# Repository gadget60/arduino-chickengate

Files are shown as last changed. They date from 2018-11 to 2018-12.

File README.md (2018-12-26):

# arduino-chickengate
Arduino based mechanic door controller

## ...what?
This is a door controller based on an Arduino. It opens a mechanic door of a hen house in the morning and closes it in the evening. That's it, basically. 

## Timing
Current date/time and open/close times are programmable via USB/serial console (need to wake up from power down sleep first by pressing one of the open or close buttons). Due to early sunset in winter time the open/close times are programmable for each month. I use a DS1307 Real Time Clock module, this allows to persist the timetable in its NVRAM.
Available commands:
- `time [hhmm]`: sets the current time
- `date [YYYYMMDD]`: sets the current date
- `gate [MM] [hhmm] [hhmm]`: sets for month MM the open and close times

## Mechanics
The door is openend/closed by a high torque gear motor, driven by a L9110 DC motor driver board. There are two buttons for manual opening/closing the door and two mechanical end switches (top and bottom).

## Power
Main issue is to keep power consumption low, because the controller as well as mechanics are driven by a small solar panel that feeds 4x1.2V rechargeable batteries. First of all, I got rid of the power LED on the ProMicro board by soldering it out. Due to high power consumption of the motor driver board, it is powered off via a transistor when not used. Finally onboard USB is disabled and the ProMicro is set to SLEEP_MODE_PWR_DOWN. Overall this brings power consumption down to around 20uA in idle mode.

## Hardware
- ProMicro Atmega 5V/16MHz (Dev-12640), https://cdn.sparkfun.com/datasheets/Dev/Arduino/Boards/ProMicro16MHzv1.pdf
- DS1307 Real Time Clock module
- L9110 DC motor driver board
- 6V high torque gear motor (ZnDiy-BRY 25GA-6V-80 DC 6V 80rpm)
- Solar panel, 0.5W, max voltage around 9V

## PINS
```
D2  --> I2C data (Realtime clock SDA)
D3  --> I2C clock (Realtime clock SCL)
D7  --> Wake up pin
D6  --> Motor A PWM Speed
D5  --> Motor A Direction
D9  --> Driver Power (Transistor Base)
D14 --> Up button, normally open
D15 --> Down button, normally open
D10 --> End switch top, normally closed
D16 --> End switch bottom, normally closed
```

## Scheme

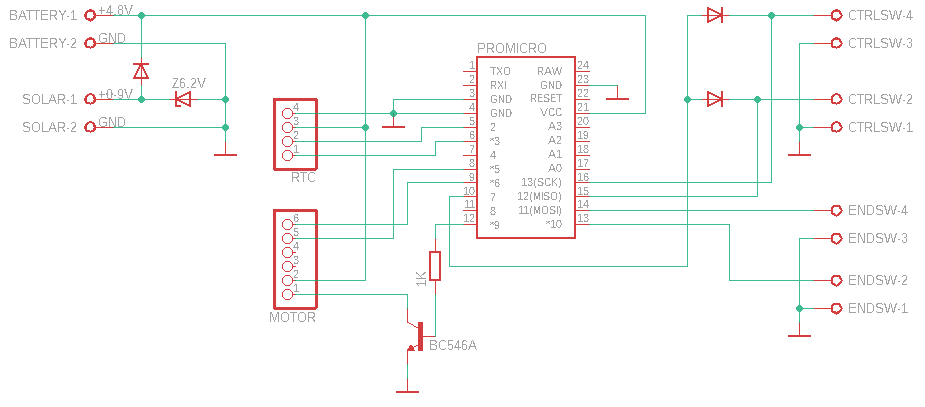
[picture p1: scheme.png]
Scheme


## Images

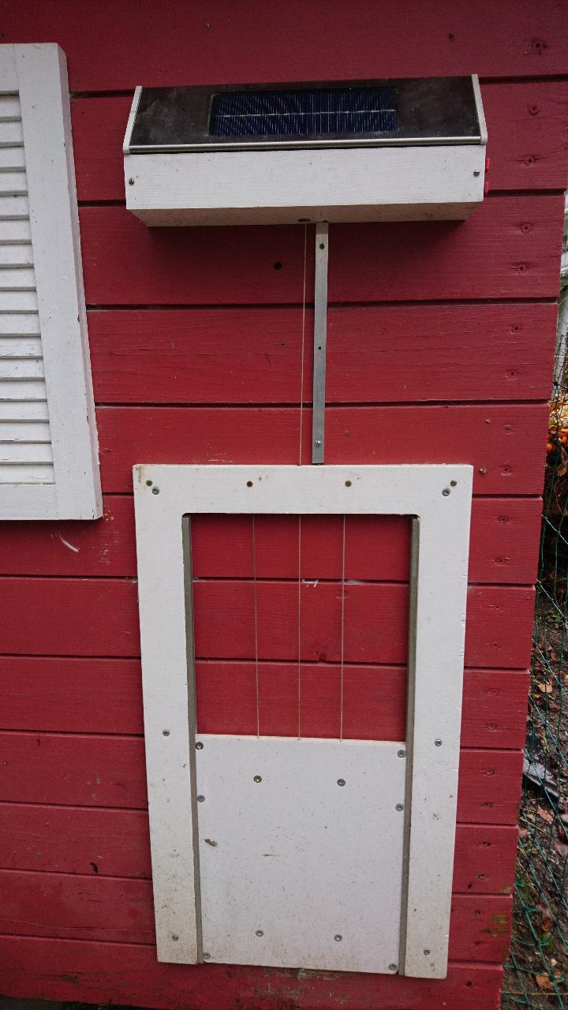
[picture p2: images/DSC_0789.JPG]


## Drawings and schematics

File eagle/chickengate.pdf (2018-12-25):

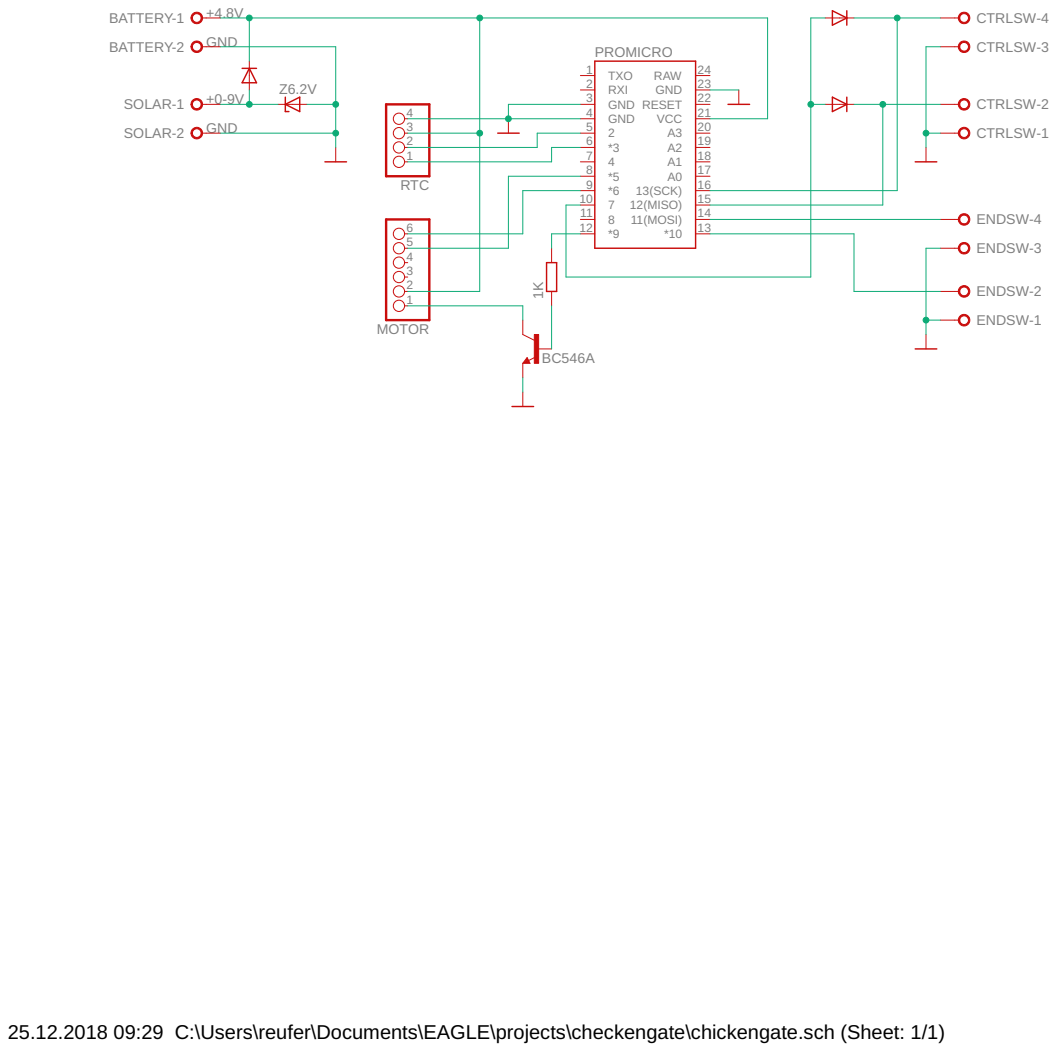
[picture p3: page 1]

25.12.2018 09:29 C:\Users\reufer\Documents\EAGLE\projects\checkengate\chickengate.sch (Sheet: 1/1)

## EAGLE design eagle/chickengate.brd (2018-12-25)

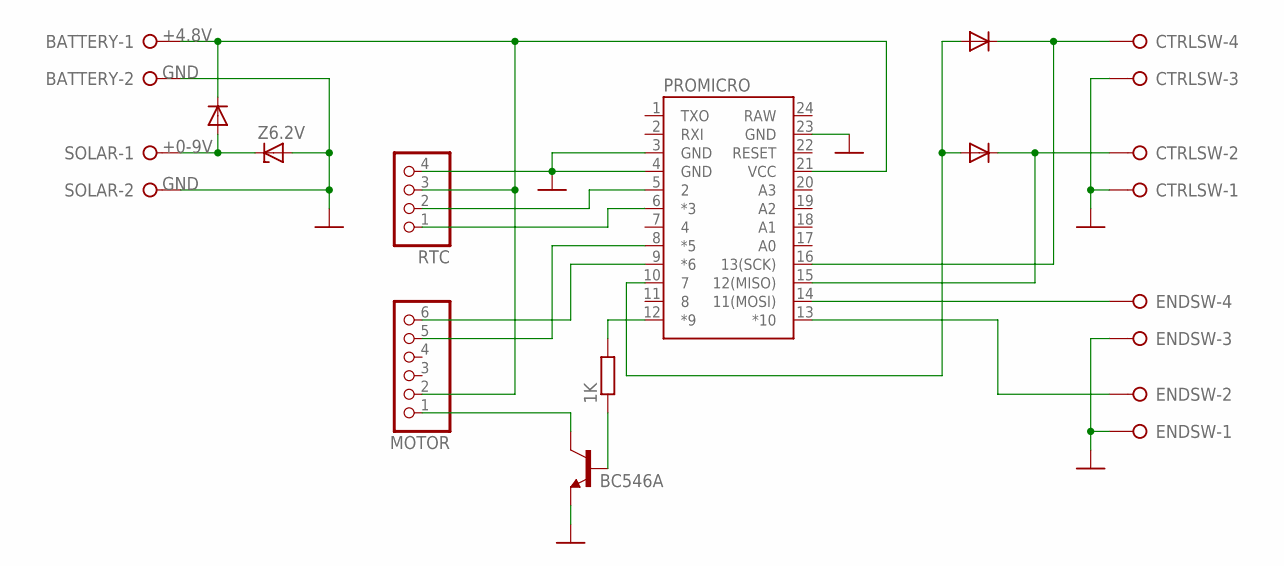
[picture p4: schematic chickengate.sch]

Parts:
1K: R-EU_0207/12; 0207/12
BATTERY: W237-02P; W237-132
CTRLSW: W237-04P; W237-4P
D1, D2, D3: 1N4004; DO41-10
ENDSW: W237-04P; W237-4P
MOTOR: PINHD-1X6; 1X06
PROMICRO: SPARKFUN_PRO_MICRO
Q1: BC546A; TO92-EBC
RTC: PINHD-1X4; 1X04
SOLAR: W237-02P; W237-132
Z6.2V: ZPD; DO35Z10

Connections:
+0-9V: D1.A, SOLAR.1, Z6.2V.C
+4.8V: BATTERY.1, D1.C, MOTOR.2, PROMICRO.21 (VCC), RTC.3
GND: BATTERY.2, CTRLSW.1, CTRLSW.3, ENDSW.1, ENDSW.3, PROMICRO.3 (GND), PROMICRO.4 (GND), PROMICRO.23 (GND), Q1.E, RTC.4, SOLAR.2, Z6.2V.A
M1: MOTOR.5, PROMICRO.8 (*5)
M2: MOTOR.6, PROMICRO.9 (*6)
unnamed: 1K.2, PROMICRO.12 (*9)
unnamed: PROMICRO.5 (2), RTC.2
unnamed: PROMICRO.6 (*3), RTC.1
unnamed: 1K.1, Q1.B
unnamed: MOTOR.1, Q1.C
unnamed: CTRLSW.4, D2.C, PROMICRO.16 (13(SCK))
unnamed: CTRLSW.2, D3.C, PROMICRO.15 (12(MISO))
unnamed: D2.A, D3.A, PROMICRO.10 (7)
unnamed: ENDSW.4, PROMICRO.14 (11(MOSI))
unnamed: ENDSW.2, PROMICRO.13 (*10)
RAW: PROMICRO.24 (RAW)

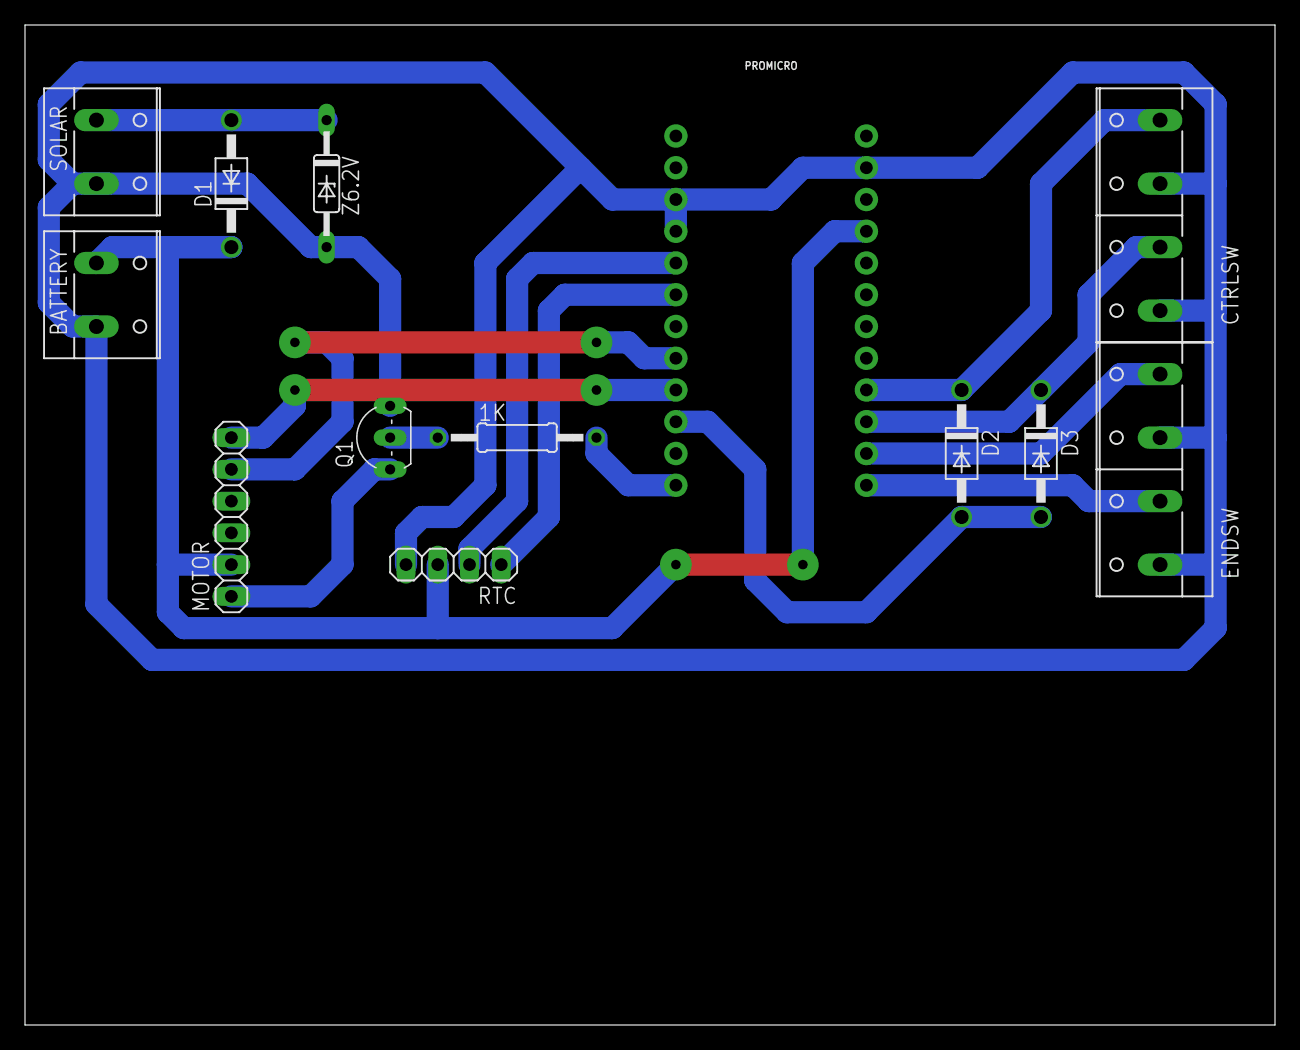
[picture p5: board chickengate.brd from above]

Board: 2 copper layers, 100.0 x 80.0 mm, 13 parts (0 on the bottom side), 15 nets.

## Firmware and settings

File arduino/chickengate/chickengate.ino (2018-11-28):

#include <avr/sleep.h>
#include <avr/power.h>
#include <avr/wdt.h>
#include <RTClib.h>
#include <Wire.h>

#define WAKE_UP_PIN 7           // D7 --> Wake up pin
#define WAKE_UP_INTERRUPT 4     // D7 INT
#define MOTOR_A_PWM 6           // D6 --> Motor B PWM Speed
#define MOTOR_A_DIR 5           // D5 --> Motor B Direction
#define MOTOR_DRIVER_POWER 9    // D9 --> Driver Power (Transistor Base)
#define BUTTON_UP 14            // D14 Up button, normally open
#define BUTTON_DOWN 15          // D15 Down button, normally open
#define ENDSWITCH_TOP 10        // D10 --> End switch top, normally closed
#define ENDSWITCH_BOTTOM 16     // D16 --> End switch bottom, normally closed

int RXLED = 17;                 // The RX LED has a defined Arduino pin
volatile bool watchdogActivated = false;
volatile bool externalActivated = false;
int sleepIterations = 0;
String inputString = "";         // a string to hold incoming data
int count = 0;                   // counter
int times[48];                   // gate open/close times

RTC_DS1307 rtc;

// external interrupt procedure
void externalWakeupProcedure()
{
  // Set the watchdog activated flag.
  externalActivated = true;
}

// watchdog timer interrupt procedure.
ISR(WDT_vect)
{
  // Set the watchdog activated flag.
  watchdogActivated = true;
}

void sleep()
{
  set_sleep_mode(SLEEP_MODE_PWR_DOWN);

  // enables the sleep bit in the mcucr register
  sleep_enable();          
  
  attachInterrupt(WAKE_UP_INTERRUPT, externalWakeupProcedure, LOW);
  
  sleep_mode();

  // zzzz...
  // here the device is actually put to sleep!!

  sleep_disable();
  
  detachInterrupt(WAKE_UP_INTERRUPT);
}


void setup(void)
{ 

  pinMode( WAKE_UP_PIN, INPUT_PULLUP);
  
  pinMode( MOTOR_A_DIR, OUTPUT );
  pinMode( MOTOR_A_PWM, OUTPUT );
  pinMode( MOTOR_DRIVER_POWER, OUTPUT );
  
  pinMode( BUTTON_UP, INPUT_PULLUP);
  pinMode( BUTTON_DOWN, INPUT_PULLUP);
  
  pinMode( ENDSWITCH_TOP, INPUT_PULLUP);
  pinMode( ENDSWITCH_BOTTOM, INPUT_PULLUP);
  
  pinMode(RXLED, OUTPUT);  // Set RX LED as an output

  digitalWrite( MOTOR_A_DIR, HIGH );
  digitalWrite( MOTOR_A_PWM, HIGH );
  digitalWrite( MOTOR_DRIVER_POWER, LOW );
  
  Serial.begin(9600);
 
  rtc.begin();

  for (int i=0; i<48; i++) {
    times[i] = rtc.readnvram(i);
  }

  Serial.println("Initializing, waiting...");

  // wait some seconds - this is just to avoid bricking the arduino
  // if something goes wrong in the wake up process
  delay(5000);

  // setup watchdog timer:
  // Note that the default behavior of resetting the Arduino
  // with the watchdog will be disabled.

  // This next section of code is timing critical, so interrupts are disabled.
  noInterrupts();

  // Set the watchdog reset bit in the MCU status register to 0.
  MCUSR &= ~(1<<WDRF);

  // Set WDCE and WDE bits in the watchdog control register.
  WDTCSR |= (1<<WDCE) | (1<<WDE);
  // Set watchdog clock prescaler bits to a value of 8 seconds.
  WDTCSR = (1<<WDP0) | (1<<WDP3);

  // Enable watchdog as interrupt only (no reset).
  WDTCSR |= (1<<WDIE);

  // Enable interrupts again.
  interrupts();
  
  Serial.println("done.");

}


void openGate()
{
  if (digitalRead(ENDSWITCH_TOP) == LOW) {
  
    digitalWrite( MOTOR_A_DIR, LOW ); 
    digitalWrite( MOTOR_A_PWM, HIGH ); 
    digitalWrite( MOTOR_DRIVER_POWER, HIGH );
  
    int i=0;
    do {
      i++;
      delay(100);

      // should not take more than 60 secounds (600 * 0.1),
      // otherwise something is probably broken...
    } while ((i<600) && (digitalRead(ENDSWITCH_TOP) == LOW) && (digitalRead(BUTTON_DOWN) == HIGH));
  
    digitalWrite( MOTOR_DRIVER_POWER, LOW );
    digitalWrite( MOTOR_A_DIR, HIGH );
    digitalWrite( MOTOR_A_PWM, HIGH );
    
    delay(500);
  }
}


void closeGate()
{
  if (digitalRead(ENDSWITCH_BOTTOM) == LOW) {
    
    digitalWrite( MOTOR_A_DIR, HIGH ); 
    digitalWrite( MOTOR_A_PWM, LOW ); 
    digitalWrite( MOTOR_DRIVER_POWER, HIGH );
  
    int i=0;
    do {
      i++;
      delay(100);

      // should not take more than 60 secounds (600 * 0.1)
      // otherwise something is probably broken...
    } while ((i<600) && (digitalRead(ENDSWITCH_BOTTOM) == LOW) && (digitalRead(BUTTON_UP) == HIGH));
    
    // wait some extra time in order to mechanically close the gate
    delay(1500);
    
    digitalWrite( MOTOR_DRIVER_POWER, LOW );
    digitalWrite( MOTOR_A_DIR, HIGH );
    digitalWrite( MOTOR_A_PWM, HIGH );
  
    delay(500);
  }
}


void printDigit(int n)
{
  if (n < 10) {
    Serial.print("0");
  }
  Serial.print(n, DEC);
}


void timeCommand(String param)
{
  DateTime newDate = rtc.now();
  if (param != "") {
    DateTime curDate = rtc.now();
    int newHour = param.substring(0,2).toInt();
    int newMin = param.substring(2).toInt();
    newDate = DateTime (curDate.year(), curDate.month(), curDate.day(), newHour, newMin, 0);
    rtc.adjust(newDate);
  }
  printDigit(newDate.hour());
  Serial.print(':');
  printDigit(newDate.minute());
  Serial.print(':');
  printDigit(newDate.second());
  Serial.println();
}

void dateCommand(String param)
{
  DateTime newDate = rtc.now();
  if (param != "") {
    DateTime curDate = rtc.now();
    int newYear = param.substring(0,4).toInt();
    int newMonth = param.substring(4,6).toInt();
    int newDay = param.substring(6).toInt();
    newDate = DateTime (newYear, newMonth, newDay, curDate.hour(), curDate.minute(), 0);
    rtc.adjust(newDate);
  }
  printDigit(newDate.day());
  Serial.print('.');
  printDigit(newDate.month());
  Serial.print('.');
  printDigit(newDate.year());
  Serial.println();
}


void gateCommand(String param)
{
  if (param != "") {
    
    int month = param.substring(0,2).toInt();
    if (month > 0 && month < 13) {
      
      int openHour = param.substring(3,5).toInt();
      int openMin = param.substring(5,7).toInt();
      int closeHour = param.substring(8,10).toInt();
      int closeMin = param.substring(10,12).toInt();  
      
      rtc.writenvram(((month - 1) * 4) + 0, openHour);
      rtc.writenvram(((month - 1) * 4) + 1, openMin);
      rtc.writenvram(((month - 1) * 4) + 2, closeHour);
      rtc.writenvram(((month - 1) * 4) + 3, closeMin);

      // re-read all from nvram
      for (int i=0; i<48; i++) {
        times[i] = rtc.readnvram(i);
      }  
    }
  }
  
  for (int i=0; i<12; i++) {
    Serial.print("Month ");
    printDigit(i + 1);
    Serial.print(": open ");
    printDigit(times[(i*4)+0]);
    Serial.print(":");
    printDigit(times[(i*4)+1]);
    Serial.print(", close ");
    printDigit(times[(i*4)+2]);
    Serial.print(":");
    printDigit(times[(i*4)+3]);
    Serial.print("\n");
  }
  
}


void onWakeupFromButton()
{
  
  delay(100);
  sei();
  USBDevice.attach(); 
  delay(100);

  Serial.begin(9600);
  delay(100);

  count = 0;
  
  while (count < 600) {

    if (digitalRead(BUTTON_DOWN) == LOW) {
      count = 0;
      Serial.print("Close gate...");
      closeGate();
      Serial.print("done.");
    }
    if (digitalRead(BUTTON_UP) == LOW) {
      count = 0;
      Serial.print("Open gate...");
      openGate();
      Serial.print("done.");
    }
    
    // process the serial input
    while (Serial.available()) {
      count = 0;
      char inChar = (char) Serial.read();

      // execute command on newline
      if (inChar == '\n') {
        
        inputString.trim();
        
        String param = "";
        String command = inputString;
        int index = inputString.indexOf(" ");
        if (index >= 0) {
          param = inputString.substring(index);
          param.trim();
          command = command.substring(0, index);
        }
        
        if (command == "time") {
          timeCommand(param);
        } else if (command == "date") {
          dateCommand(param);
        } else if (command == "gate") {
          gateCommand(param);
        } else {
          Serial.println("Unknown command " + command);
          Serial.println("Available commands are:");
          Serial.println("- time [<hhmm>]");
          Serial.println("- date [<YYYYMMDD>]");
          Serial.println("- gate [<MM> <hhmm> <hhmm>]");
        }
        
        inputString = "";

      } else {

        // add it to the inputString:
        inputString += inChar;

      }
    }
     
    delay(100);
    count++; 
  }
  
  Serial.println("Timer: Entering Sleep mode after 60 seconds inactivity");

  // this delay is needed, the sleep
  // function will provoke a Serial error otherwise!!
  delay(100);     
                  
  // detach the USB
  USBCON |= _BV(FRZCLK);  //freeze USB clock
  PLLCSR &= ~_BV(PLLE);   // turn off USB PLL
  USBCON &= ~_BV(USBE);   // disable USB  

}


void onWakeupFromTimer()
{
  sleepIterations++;
  
  // make sure at least once a minute:
  if (sleepIterations >= 3) {

    digitalWrite(RXLED, LOW);
    delay(50);
    digitalWrite(RXLED, HIGH);

    DateTime curDate = rtc.now();
    int i = ( curDate.month() - 1) * 4;
    
    if (curDate.hour() == times[i + 0] && curDate.minute() == times[i + 1]) {
      openGate();
    }
    if (curDate.hour() == times[i + 2] && curDate.minute() == times[i + 3]) {
      closeGate();
    }

    // security setting: always close the door at 22pm
    if (curDate.hour() == 22 && curDate.minute() == 00) {
      closeGate();
    }

    sleepIterations = 0;
    // do something
  } 
}



void loop(void)
{

  // detach the USB
  USBCON |= _BV(FRZCLK);  // freeze USB clock
  PLLCSR &= ~_BV(PLLE);   // turn off USB PLL
  USBCON &= ~_BV(USBE);   // disable USB  

  while(true) {
    
    if (watchdogActivated) {
      // timer interrupt 
      onWakeupFromTimer();
      watchdogActivated = false;
    }    
    
    if (externalActivated) {
      // external interrupt
      onWakeupFromButton();
      externalActivated = false;
    }
    
    if (watchdogActivated == false && externalActivated == false) {
      sleep();
    }
 
  }

}

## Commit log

2018-11-28 fix pin description
2018-12-25 add schema
    [chickengate.brd, chickengate.sch]

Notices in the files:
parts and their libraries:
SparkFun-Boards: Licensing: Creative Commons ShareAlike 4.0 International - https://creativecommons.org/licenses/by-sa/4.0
